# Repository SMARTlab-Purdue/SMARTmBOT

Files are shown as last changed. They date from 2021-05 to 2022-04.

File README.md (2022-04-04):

# SMART lab multi-roBOT (SMARTmBOT)
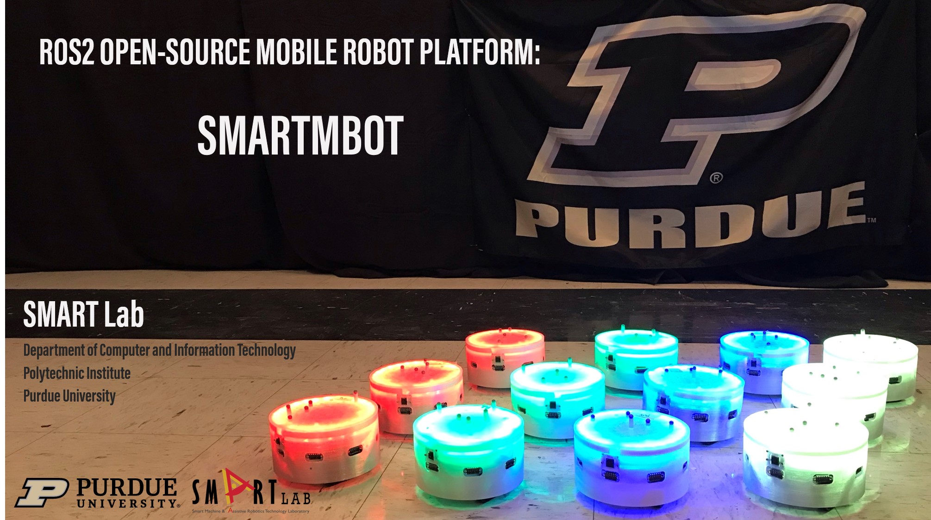
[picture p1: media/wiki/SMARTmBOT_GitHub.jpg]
GitHub markdown


## Objectives
The goal of this repository is to introduce a new, customizable, scalable, and fully opensource mobile robot platform, called SMARTmBOT (v2022). In this repository, we provide a detailed tutorial, and all design files and source codes so that you can build your own SMARTmBOT with off-the-shelf components and also customize its design and functionalities according to your needs. SMARTmBOT supports a new Robot Operating System 2 (ROS2) on Raspberry Pi 4, and we expect SMARTmBOT to be definitely useful for studying the basics of robotics, especially mobile robotics. SMARTmBOT can also be used to study advanced topics such as swarm robotics.

## Wiki, Tutorial, and Demonstrations
Please refer to our [Wiki page](https://github.com/SMARTlab-Purdue/SMARTmBOT/wiki) for a detailed tutorial on SMARTmBOT. The content of the tutorial is as follows:

1. [Basic ROS2 Example](https://github.com/SMARTlab-Purdue/SMARTmBOT/wiki/1.-Basic-ROS2-Example)

2. [Build SMARTmBOT (Hardware)](https://github.com/SMARTlab-Purdue/SMARTmBOT/wiki/2.-Build-SMARTmBOT-(Hardware))

3. [Build SMARTmBOT (Software)](https://github.com/SMARTlab-Purdue/SMARTmBOT/wiki/3.-Build-SMARTmBOT-(Software))

4. [SMARTmBOT Examples](https://github.com/SMARTlab-Purdue/SMARTmBOT/wiki/4.-SMARTmBOT-Examples)

You can also read or download a PDF version of [SMARTmBOT Guide/Manual](https://github.com/SMARTlab-Purdue/SMARTmBOT/blob/main/Documents/SMARTmBOT_Manual.pdf), and watch a full demo video of the SMARTmBOT at <https://youtu.be/uniaTWcCeDM>.

## Contact
If you have any questions or find any issues on SMARTmBOT, please feel free to contact us. We will fix and update them as soon as possible.

## Contributors
All of the contributors are with [SMART Lab](http://www.smart-laboratory.org/index.html), Department of Computer and Information Technology, Purdue University, West Lafayette, IN 47907, USA.<br />

<table>
  <tr>

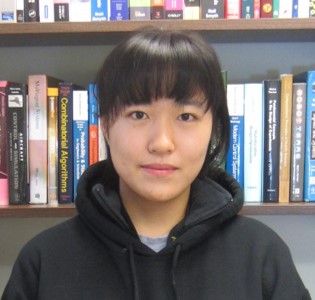
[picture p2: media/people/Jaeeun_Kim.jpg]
<td align="center"><a href="http://www.smart-laboratory.org/group/Jaeeun_Kim.html"><br />
              <sub><b><a href="http://www.smart-laboratory.org/group/Jaeeun_Kim.html" title="personal_website">🌍Jaeeun Kim</b></sub></a><br />
<sub><b>Software</b></sub></a><br />
<sub><b><a href="mailto: kim2592@purdue.edu" title="contact">kim2592@purdue.edu </a></b></sub></a><br />

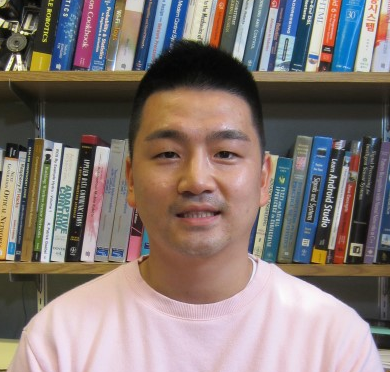
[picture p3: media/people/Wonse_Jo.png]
<td align="center"><a href="http://www.smart-laboratory.org/group/Wonse_Jo.html"><br />
          <sub><b><a href="http://www.smart-laboratory.org/group/Wonse_Jo.html" title="personal_website">🌍Wonse Jo</b></sub></a><br />
<sub><b>Hardware</b></sub></a><br />
<sub><b><a href="mailto: jow@purdue.edu" title="contact">jow@purdue.edu</a></b></sub></a><br />
</td>
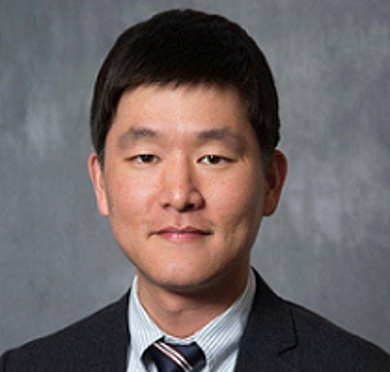
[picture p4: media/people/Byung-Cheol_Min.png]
<td align="center"><a href="http://www.smart-laboratory.org/group/bcm.html"><br />
  <sub><b><a href="http://www.smart-laboratory.org/group/bcm.html" title="personal_website">🌍Byung-Cheol Min</b></sub></a><br />
<sub><b>Director</b></sub></a><br />
<sub><b><a href="mailto: minb@purdue.edu" title="contact">minb@purdue.edu</a></b></sub></a><br />

  </tr>

</table>

## Acknowledgement

This material is based upon work supported by the National Science Foundation under [Grant No. IIS-1846221](https://www.nsf.gov/awardsearch/showAward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). Any opinions, findings, and conclusions or recommendations expressed in this material are those of the author(s) and do not necessarily reflect the views of the National Science Foundation.

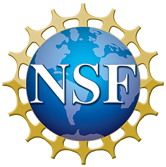
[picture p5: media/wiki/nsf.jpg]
NSF_image


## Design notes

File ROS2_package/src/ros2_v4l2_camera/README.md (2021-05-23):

# v4l2_camera

A ROS 2 camera driver using Video4Linux2 (V4L2).

## Installation
[This article](https://medium.com/swlh/raspberry-pi-ros-2-camera-eef8f8b94304) details how to build and run this package. It focuses on Raspberry Pi OS with the Raspberry Pi Camera Module V2 but should generalise for most systems.

### ROS package install
This is available from the ROS package repositories and can therefore be installed with the following command and your ROS version name:

    apt-get install ros-<ros_version>-v4l2-camera

### Building from source
If you need to modify the code or ensure you have the latest update you will need to clone this repo then build the package.

    $ git clone --branch foxy https://gitlab.com/boldhearts/ros2_v4l2_camera.git src/v4l2_camera
    $ colcon build

Most users will also want to set up compressed transport using the dependencies below.

### Usage
Publish camera images, using the default parameters:

        ros2 run v4l2_camera v4l2_camera_node

Preview the image (open another terminal):

        ros2 run rqt_image_view rqt_image_view

## Dependencies

* `image_transport` - makes it possible to set up compressed transport
  of the images, as described below.

    The ROS 2 port of `image_transport` in the `image_common`
    repository is needed inside of your workspace:

        git clone --branch ros2 https://github.com/ros-perception/image_common.git src/image_common

    Note that `image_transport` only supports raw transport by default
    and needs additional plugins to actually provide compression; see
    below how to do this.

## Nodes

### v4l2_camera_node

The `v4l2_camera_node` interfaces with standard V4L2 devices and
publishes images as `sensor_msgs/Image` messages.

#### Published Topics

* `/raw_image` - `sensor_msgs/Image`

    The image.

#### Parameters

* `video_device` - `string`, default: `"/dev/video0"`

    The device the camera is on.

* `pixel_format` - `string`, default: `"YUYV"`

    The pixel format to request from the camera. Must be a valid four
    character '[FOURCC](http://fourcc.org/)' code [supported by
    V4L2](https://linuxtv.org/downloads/v4l-dvb-apis/uapi/v4l/videodev.html)
    and by your camera. The node outputs the available formats
    supported by your camera when started.  
    Currently supported: `"YUYV"` or `"GREY"`

* `output_encoding` - `string`, default: `"rgb8"`

    The encoding to use for the output image.  
    Currently supported: `"rgb8"`, `"yuv422"` or `"mono8"`.

* `image_size` - `integer_array`, default: `[640, 480]`

    Width and height of the image.

* Camera Control Parameters

    Camera controls, such as brightness, contrast, white balance, etc,
    are automatically made available as parameters. The driver node
    enumerates all controls, and creates a parameter for each, with
    the corresponding value type. The parameter name is derived from
    the control name reported by the camera driver, made lower case,
    commas removed, and spaces replaced by underscores. So
    `Brightness` becomes `brightness`, and `White Balance, Automatic`
    becomes `white_balance_automatic`.

## Compressed Transport

By default `image_transport` only supports raw transfer, plugins are
required to enable compression. Standard ones are available in the
[`image_transport_plugins`](https://github.com/ros-perception/image_transport_plugins)
repository. These depend on the OpenCV facilities provided by the
`vision_opencv` repository. You can clone these into your workspace to
get these:

    cd path/to/workspace
    git clone https://github.com/ros-perception/vision_opencv.git --branch ros2 src/vision_opencv
    git clone https://github.com/ros-perception/image_transport_plugins.git --branch ros2 src/image_transport_plugins

### Building: Ubuntu

The following packages are required to be able to build the plugins:

    sudo apt install libtheora-dev libogg-dev libboost-python-dev

### Building: Arch

To get the plugins compiled on Arch Linux, a few special steps are
needed:

* Arch provides OpenCV 4.x, but OpenCV 3.x is required
* Arch provides VTK 8.2, but VTK 8.1 is required
* `boost-python` is used, which [needs to be linked to python libs
  explicitly](https://bugs.archlinux.org/task/55798):

        colcon build --symlink-install --packages-select cv_bridge --cmake-args "-DCMAKE_CXX_STANDARD_LIBRARIES=-lpython3.7m"

### Usage

If the compression plugins are compiled and installed in the current
workspace, they will be automatically used by the driver and an
additional `/image_raw/compressed` topic will be available.

Neither Rviz2 or `showimage` use `image_transport` (yet). Therefore, to
be able to view the compressed topic, it needs to be republished
uncompressed. `image_transport` comes with the `republish` node to do
this:

    ros2 run image_transport republish compressed in/compressed:=image_raw/compressed raw out:=image_raw/uncompressed

The parameters mean:

* `compressed` - the transport to use for input, in this case
  'compressed'. Alternative: `raw`, to republish the raw `/image_raw`
  topic
* `in/compressed:=image_raw/compressed` - by default, `republish` uses
  the topics `in` and `out`, or `in/compressed` for example if the
  input transport is 'compressed'. This parameter is a ROS remapping
  rule to map those names to the actual topic to use.
* `raw` - the transport to use for output. If omitted, all available
  transports are provided.
* `out:=image_raw/uncompressed` - remapping of the output topic.

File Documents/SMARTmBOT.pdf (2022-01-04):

## A ROS2-based Swarm Robot Platform: SMARTmBOT

Jaeeun Kim, Wonse Jo, and Byung-Cheol Min

Abstract— This paper is to introduce a new open-source swarm robot platform for a multi-robot research applications. The mobile robot is 15 cm in diameter and 10 cm in height and supports the Robot Operating System 2 (ROS2). The hardware is composed of three layers of printed circuit board (PCB). The first PCB layer has two DC motors with a motor driver chip (L293D), and two line sensors to detect cliffs or black lines. The second PCB layer is to connect with a Raspberry Pi and eight times-of-flight (ToF) sensors to detect surrounding obstacles. The third PCB layer is customizable. In our case, we mounted four RGB SMD LEDs (SMD5050), RGB LED strips (WS2913b), and a speaker on the thrid PCB layer. Therefore, the robot platform is able to change its light either individually or as a whole, play music, and measure the distance of nearby obstacles using ToF sensors. Furthermore, we provide all source codes and design files used on the mobile robot platform.

I. INTRODUCTION

Swarm robotics is a potential field that can solve complex and difficult challenges in robotics applications. Various robot platforms have been introduced by companies and research groups for swarm robotics.
To address these challenges, various research institutes, universities, and companies have been launching various STEM tools. An example of the mobile robot platforms is Donkey Car, which provides the learning tools for driving an RC car and process data collected with it [1]. Similarly, Miniskybot aims to be a learning tool that is cheap and easy to build [2]. It has 3D printed parts and its own processing board, which is controlled by a personal computer. Although there are aforementioned mobile platforms that allow the user to build from scratch and modify as they need, there is still a huge barrier for students to learn STEM educations, as well as for the researchers who are not in robotics to conduct human-robot interaction (HRI).
However, those platforms are still expensive and limited in expandability for other research to use.
Therefore, we propose a new fully open-source swarm robot platform, called SMARTmBOT that can be used for swarm research purposes. The SARTmBOT is made with a 3D printed casing and using a Raspberry Pi 4 installed Robot Operating System 2 (ROS2) [3] to control the devices and read sensors mounted on three layers of the printed circuit board (PCB). The sensors and visual output components are mounted on the PCBs, such as RGB LEDs, Time of Flight (ToF) sensors, photo reflector sensors (also known as a line sensor), and DC gear motors. The power source for

Jaeeun Kim, Wonse Jo, and Byung-Cheol Min are with SMART Lab, Department of Computer and Information Technology, Purdue University, West Lafayette, IN 47907, USA kim2592@purdue.edu, jow@purdue.edu, minb@purdue.edu

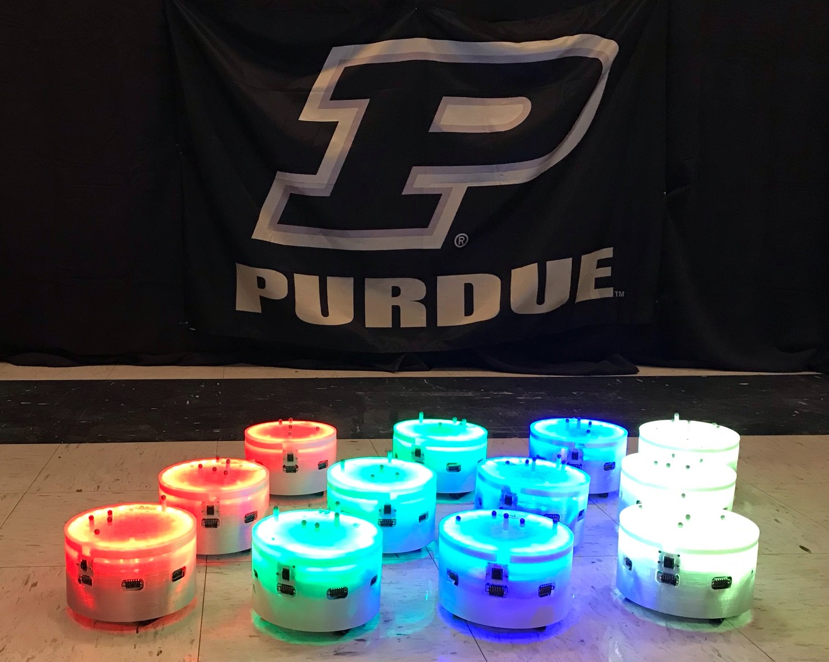
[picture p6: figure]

Fig. 1: SMARTmBOT platforms mounted a WS2813B RGB LED strip to change the overall case.

SMARTmBOT is a portable power bank, and the rest of the sensors and components are powered by the Raspberry Pi 4. As well, we elaborated specific details of software in Section III.

II. HARDWARE
The components used in the SMARTmBOT are shown in Table I, composed of off-the-shelf items. The cost for building a SMARTmBOT is about $ 250. Furthermore, in order to assist those who are building the robot, a video to introduce how to solder and assembly the platform is available. To find the video, please go to this link: https:
//youtu.be/hEa0x9cL72s
A. 3D designs
The SMARTmBOT is 15 cm in diameter and 10 cm in height, and composed of 3D printed parts as shown in Figure 3. All parts should be completely printed and soldered before assembling them. Figure 3a is a transparent case to cover the whole robot platform and illuminate color lights using RGB LEDs. Figure 3b is a power bank holder that serves as the main base of the SMRTmBOT. The part is to mount the power bank and connect other PCB layers and Raspberry Pi 4. Figure 3c is a motor mount bracket to fix two DC motors. The perforated hole is to pass and arrange a power cable and cables of the DC motors. Figure 3d is a shaft support bracket to fasten the the shaft of belt chain on the power bank holder. Figure 3e is a motor mount bracket to fix a Pi camera

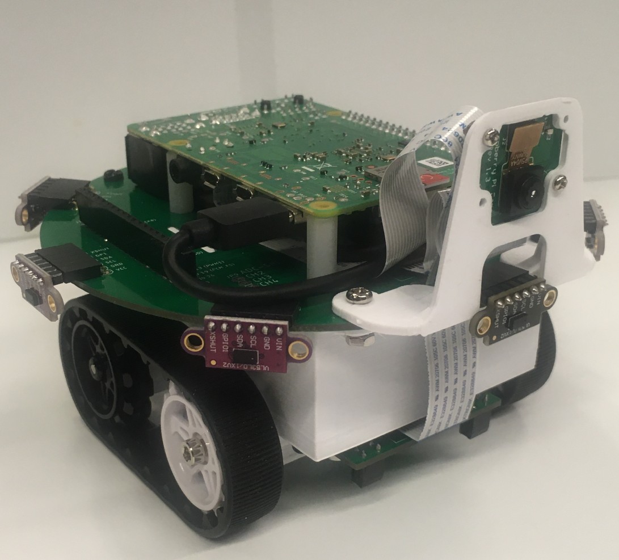
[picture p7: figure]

Fig. 2: Basic version of the SMARTmBOT platform.

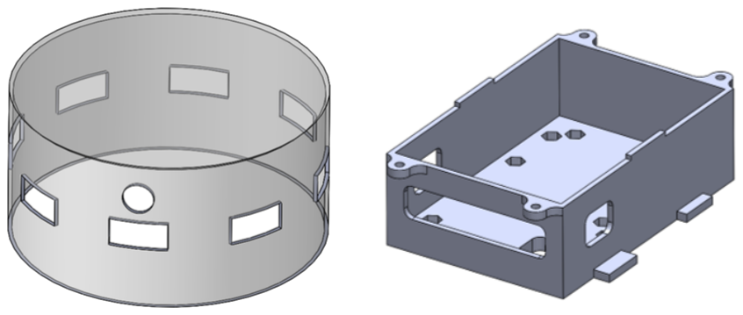
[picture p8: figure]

(a) (b)
(c) | (d) | (e)

Fig. 3: 3D printing parts for SMARTmBOT; (a) Transparent case (1EA), (b)Power bank holder, (c) Motor mount bracket,
(d) Shaft support bracket, and (e) Camera holder.

on the second PCB layer. All design and 3D printing files can be downloaded from: https://github.
com/SMARTlab-Purdue/SMARTmBOT/tree/main/ Hardware_design/3DprintingParts.
B. PCB design
1) First Layer: The first PCB layer shown in Figure 4a is located between the wheels, facing downwards. It includes a motor driver (L293D), ADC-SPI chip (MCP3008), and two photo reflector sensors (RPR220). Motor lines and external power supply from the battery is connected to this layer.
2) Second Layer: The second layer is placed on top of the battery housing, holding mounts for Raspberry Pi and ToF sensors.
3) Third Layer: The third layer is placed on top of the second layer, connected by pin headers.
4) Custom Layer: This layer provides extra pins on the third layer PCB to connect an additional layers.

TABLE I: BOM list for the SMARTmBOT

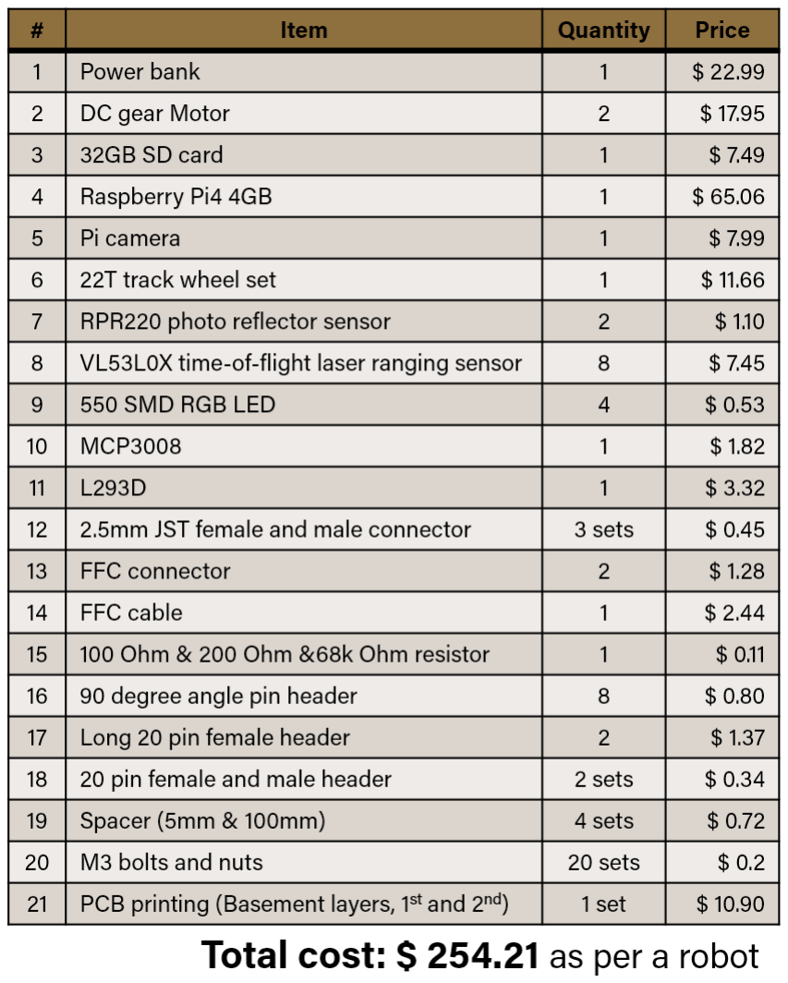
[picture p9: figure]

III. SOFTWARE

The software required to run the ROS2 packages are available for download at https://github.com/
SMARTlab-Purdue/smart_mbot_ws. (https://github.com/SMARTlab-Purdue/smart_mbot_ws) The system runs
on Ubuntu 20.04 Server and ROS2 Galactic.
A. Control the LEDs with GPIO Pins

The LEDs can emit red, green, or blue light. Each color is connected to a separate GPIO pin, so the user can turn individual or multiple colors at the same time. The pins used for the LEDs are 7, 8, and 25. Below is the part of LED code included in the package. To control the LED colors, set the output of the wanted color’s pin to HIGH by changing the GPIO.LOW to GPIO.HIGH.

Code 1: Python example

1 GPIO.output(pin, GPIO.LOW)

B. Read ADC via SPI Node

The photo reflector sensors used in this robot, RPR220, are analog sensors which signals are converted into digital signals and read on SPI bus via MCP3008 chip. The pin used for the sensor is 5.
The code in the package will convert the analog data to voltage values, stored in an array. Below is the part of the

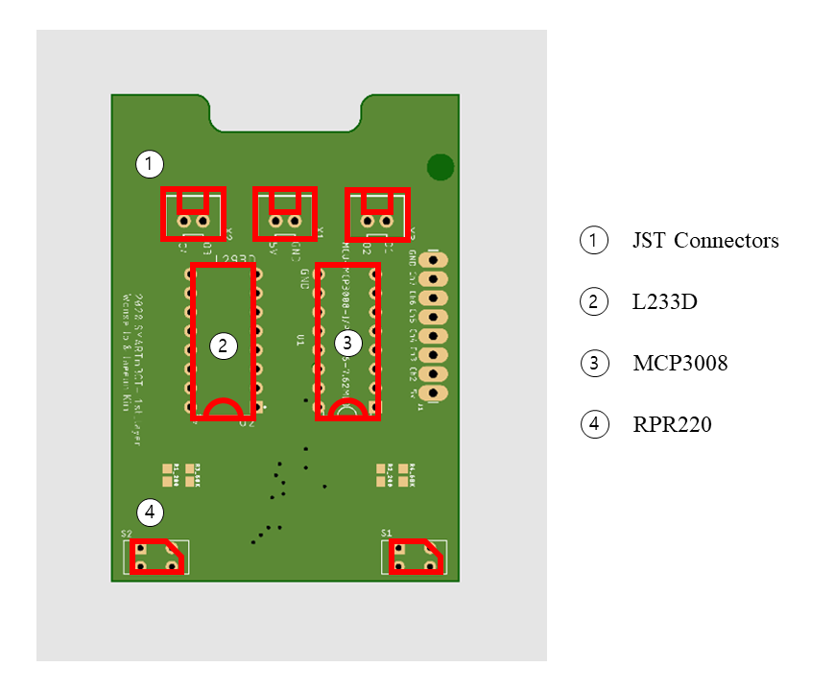
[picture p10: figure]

(a) First PCB layer

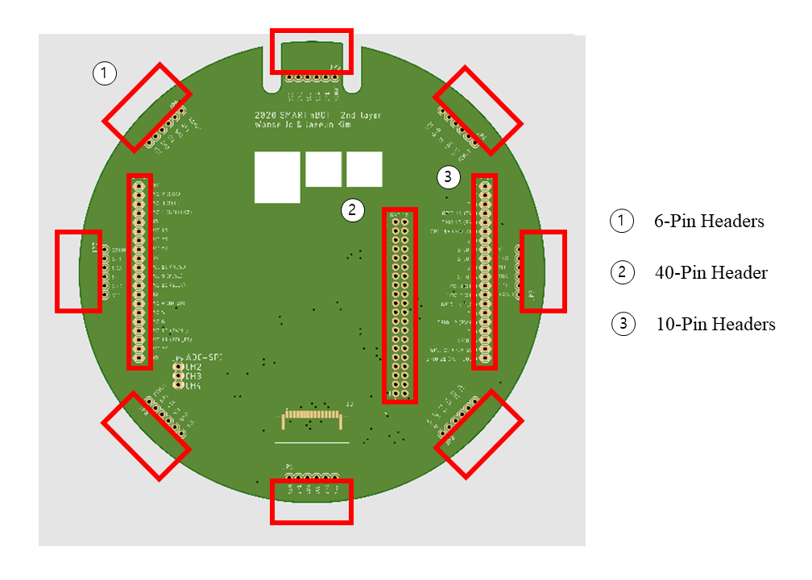
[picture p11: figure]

(b) Second PCB layer

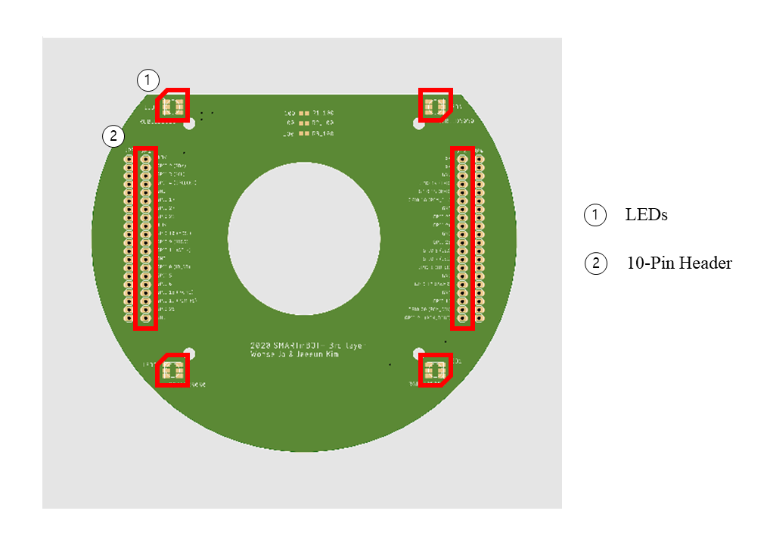
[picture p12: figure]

(c) Third PCB layer

Fig. 4: Gerber design files for the PCB layers;

code used for reading data from the sensors. The data is automatically published as ROS2 message Float32MultiArray as ’smartmobil/ADC’.

Code 2: Python example

1 | # Initialize and define Publishers
2 | self.pub_adc_spi_reader = self.create_publisher(
| Float32MultiArray, ’smartmobil/ADC’, 10)

3
4 | # Setting timer for publisher
5 | pub_adc_spi_reader_timer_period = 0.001 #sec
6 | self.pub_adc_spi_reader_timer =
7 | self.create_timer(pub_adc_spi_reader_timer_period,
| self.pub_adc_spi_reader_timer_callback)

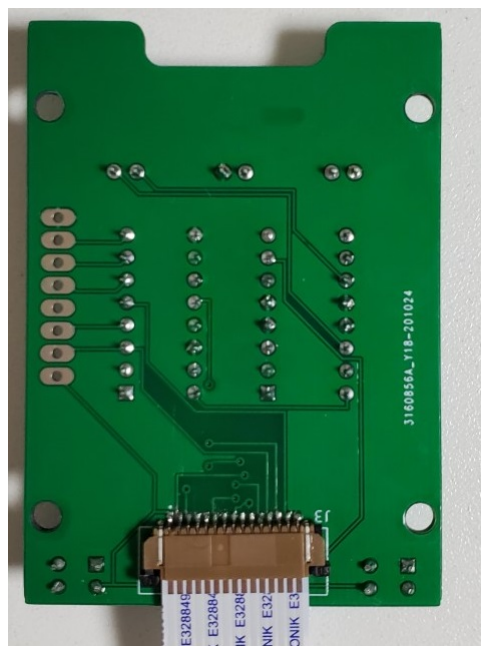
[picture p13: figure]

(a) Back of the first layer

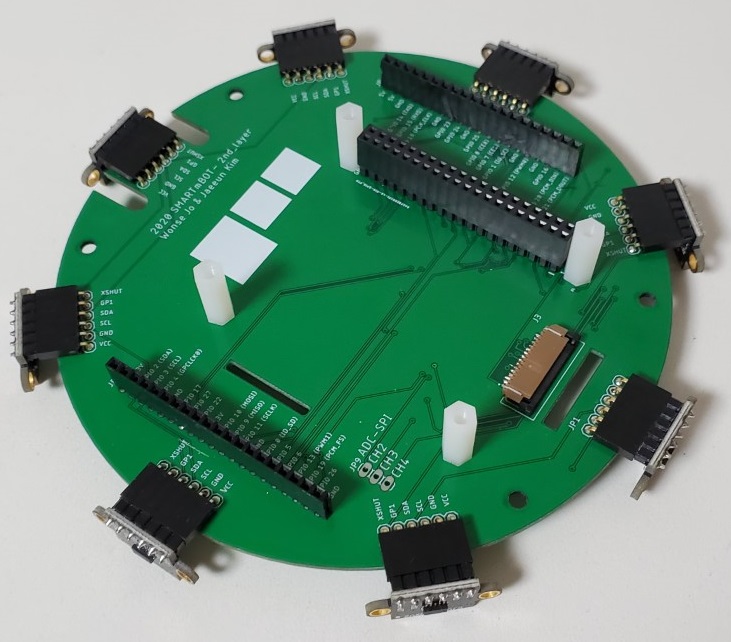
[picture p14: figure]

(b) Isometric view of the second layer

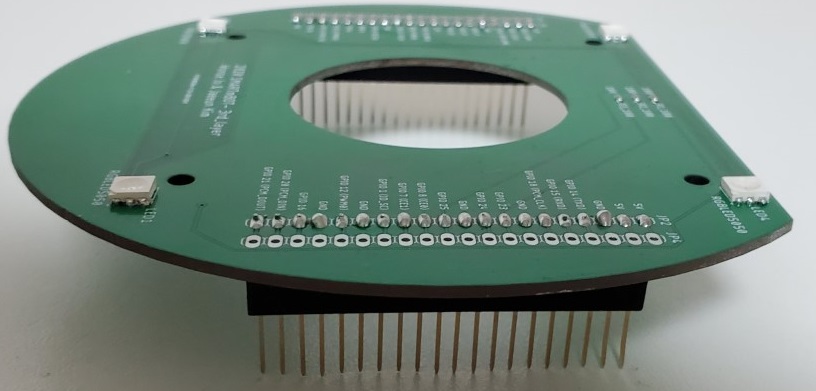
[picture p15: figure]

(c) Isometric view of the third view

Fig. 5: Three simple graphs

C. Control DC Motors
We used L293D motor driver chip to control two DC motors with pulse-width modulation (PWM). The pins used for first motor is 37, 33, 35, and second motor is 36, 38,
40. The last pins listed in each motors are used for PWM control.
The code below is displaying the equation used to calculate each wheel’s velocity with given linear and angular velocity. WHEEL BASE is the distance between the two wheels and WHEEL RADIUS is the radius of the wheel.

Code 3: Python example

1 self.right_velocity = abs((self.lin_vel - self. ang_vel * WHEEL_BASE / 2.0) / WHEEL_RADIUS)

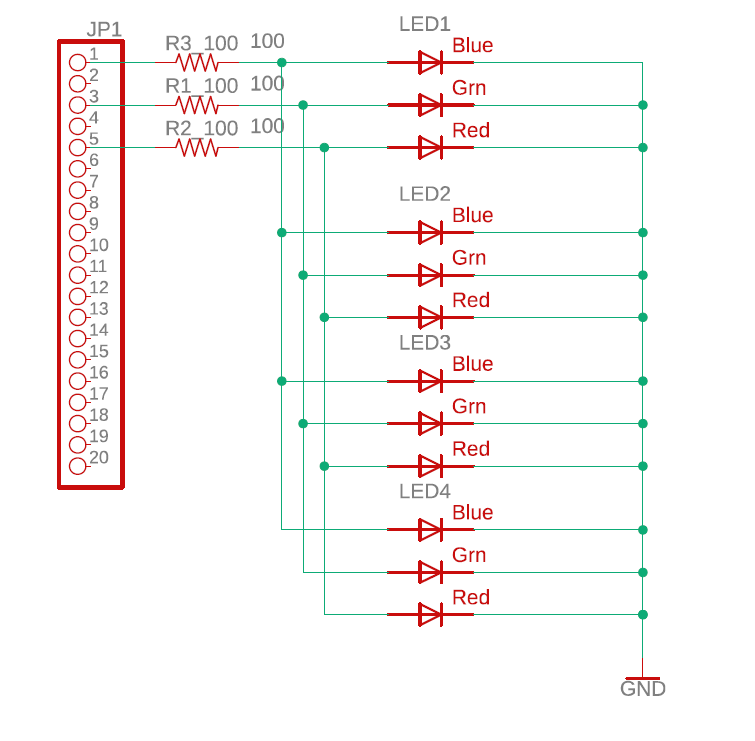
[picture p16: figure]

Fig. 6: Schematic of four LEDs (not an exhaustive diagram)

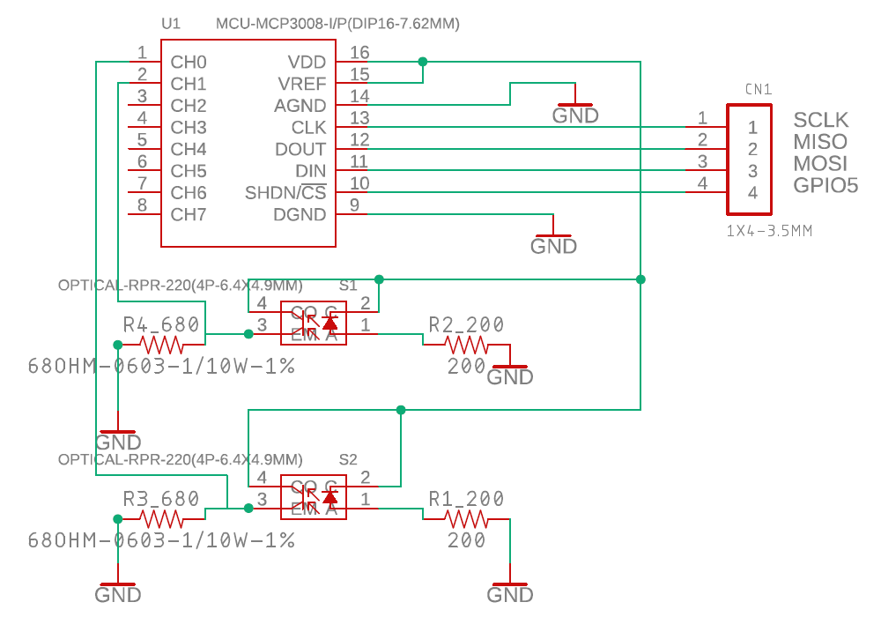
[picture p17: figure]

Fig. 7: Schematic of SPI-ADC wiring with photo reflector sensors (not an exhaustive diagram)

2 self.left_velocity = abs((self.lin_vel + self. ang_vel * WHEEL_BASE / 2.0) / WHEEL_RADIUS)

D. Read ToF Sensors
The eight ToF sensors or on a I2C bus, each with their unique I2C addresses. The pins used for the sensors are 13, 18, 16, 15, 12, 11, 8, and 10.
Below is the part of the code used for reading data from the sensors. The data is automatically published as ROS2 message Int32MultiArray as ’smartmobil/I2C’.

Code 4: Python example

1 | # Initialize the I2C module
2 | self.i2c = board.I2C()
3 | self.pub_i2c_tof_reader = self.create_publisher( Int32MultiArray, ’smartmobil/I2C’, 10)

IV. ROS 2 LAUNCH
Code 5 is a ROS2 launch file to run a group of nodes at a same time. For this application, the launch file included in the package runs motor, SPI, I²C, and LED strip nodes together.

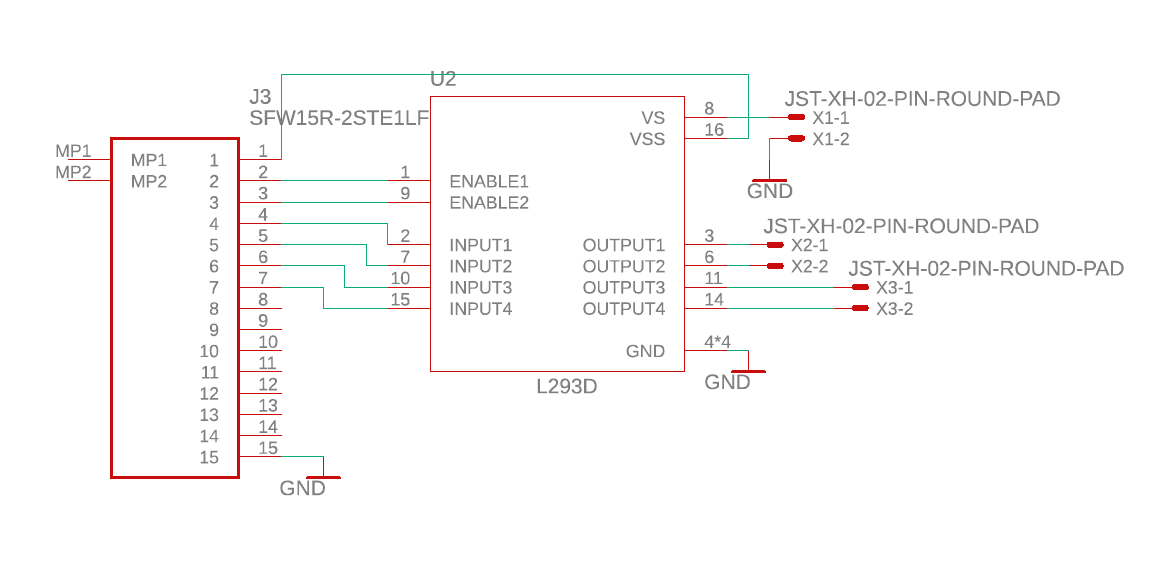
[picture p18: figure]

Fig. 8: Schematic of motor driver with two DC motors and an external power source (not an exhaustive diagram)

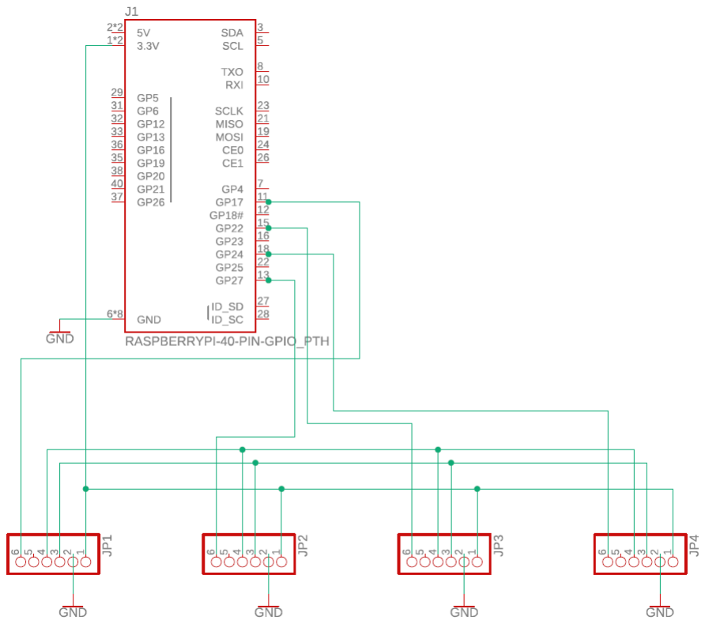
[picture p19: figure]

Fig. 9: Schematic of I2C wiring with four ToF sensors (not an exhaustive diagram)

Code 5: Launch file to control SMARTmBOT

1 import numpy as np

To launch the package, type the following commands to the terminal:

1 | $cd ˜/smart_mbot_ws
2 | $colcon build
3 | $source install/setup.bash
4 | $ros2 launch smart_mbot_pkg $smart_mbot_pkg.launch.
| py

There are two subscribers and two publishers in the package. Since they are in ROS2 message formats, the user can write to the publisher and read the publishers by accessing the topics with appropriate messages. The topics are listed and explained further in Table II and Table III.
As an example, it is possible to directly publish a message

TABLE II: ROS2 Topic Subscriber List

Name | Type | Description
/writing dc motor vel | Float32MultiArray | Linear and Angular Velocity for the Motors
/writing ws2813 rgb strip | Float32MultiArray | LED Strip Parameters

TABLE III: ROS2 Topic Publisher List

Name | Type | Description
VL53L0X tof /reading i2c | Int32MultiArray | Array of ToF Sensor Values
/reading spi adc | Float32MultiArray | Array of Photo Reflector Sensor Values

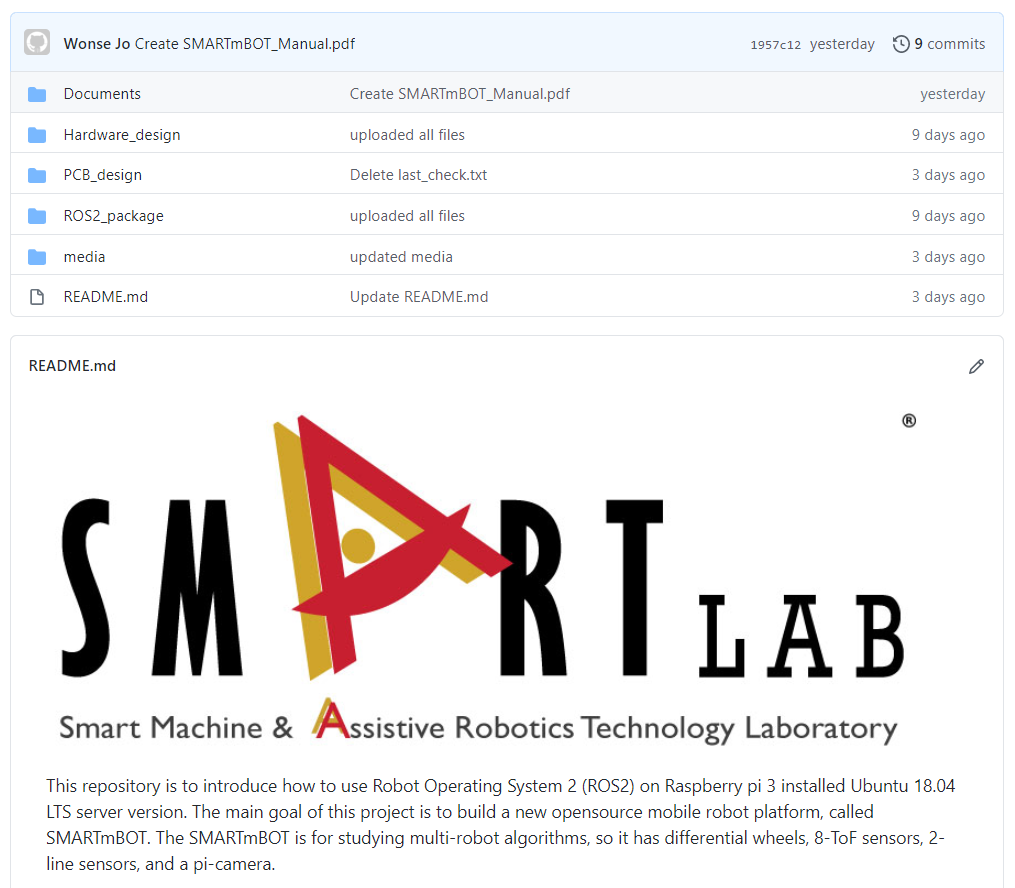
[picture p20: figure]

Fig. 10: SMARTmBOT GitHub page

to /writing dc motor vel to control the motors. The message type Float32MultiArray accepts right and left motor velocities as a form of ”data: [right motor pwm(-255 255), left motor pwm(-255 255)]”. When running in the terminal, the command should look like Code 6.

Code 6: Controlling motors of SMARTmBOT

1 | ros2 topic pub /<robot_name>/writing_dc_motor_vel std_msgs/msg/Float32MultiArray "data: [100,100]
| "
V. ONLINE REPOSITORIES
The GitHub repository can be found in the following
link: https://github.com/SMARTlab-Purdue/
SMARTmBOT. (https://github.com/SMARTlab-Purdue/SMARTmBOT) In the repository, there are 3D design CAD files, PCB design files, and ROS2 package utilized on the SMARTmBOT. The 3D design files are created by SolidWorks 2020, the PCB designs are created by AutoDesk Eagle CAD, and ROS2 nodes are written using Python 3.8.
| VI. CONCLUSION AND FUTURE WORKS
In this paper, we presented an open-source mobile robot platform to serve as a learning tool for K-12 student. The components are relatively cheap and mainstream so that they are easy to obtain, and this manual will help the students to assemble and modify the codes.
In the future, we will conduct a new user study to investigate the effect of the multi-robot system on human perception and cognition. And also, we will share the mobile platform with K-12 students to give opportunities to learn human-robot interaction via virtual meeting and/or in-person meeting.

ACKNOWLEDGMENT
This material is based upon work supported by the National Science Foundation under Grant No. IIS-1846221. Any opinions, findings, and conclusions or recommendations expressed in this material are those of the author(s) and do not necessarily reflect the views of the National Science Foundation.

REFERENCES

[1] Autorope, “donkeycar,” https://github.com/autorope/donkeycar, 2020.
[2] J. Gonzalez-Gomez, A. Valero-Gomez, A. Prieto-Moreno, and M. Abderrahim, “A new open source 3d-printable mobile robotic platform for education,” in Advances in autonomous mini robots. Springer, 2012, pp. 49–62.
[3] “Ros 2 documentation¶.” [Online]. Available: https://index.ros.org/doc/ros2/ (https://index.ros.org/doc/ros2/)

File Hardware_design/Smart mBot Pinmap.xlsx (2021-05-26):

1 | 3.3V | 5V | 2 | MOTOR
3 | SDA | 5V | 4 | SPI
5 | SCL | GND | 6 | LED
7 | 4 | 14 | 8 | I2C
9 | GND | 15 | 10 | RGB Strip
11 | 17 | 18 | 12
13 | 27 | GND | 14
15 | 22 | 23 | 16
17 | 3.3V | 24 | 18
19 | 10 | GND | 20
21 | 9 | 25 | 22
23 | 11 | 8 | 24
25 | GND | 7 | 26
27 | 0 | 1 | 28
29 | 5 | GND | 30
31 | 6 | 12 | 32
33 | 13 | GND | 34
35 | 19 | 16 | 36
37 | 26 | 20 | 38
39 | GND | 21 | 40

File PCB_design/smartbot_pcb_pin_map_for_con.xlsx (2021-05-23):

 | 1st layer to 2nd layer X1@2nd layer |  | 2nd layer to 3rd layer X2@2nd layer
P-1 | 5V | P-1 | 5V
P-2 | M1-enable | P-2 | 3.3V
P-3 | M1-input1 | P-3 | SDA
P-4 | M1-input2 | P-4 | SCL
P-5 | M2-enable | P-5 | SCLK(CLK)
P-6 | M2-input3 | P-6 | MISO(DOUT)
P-7 | M2-input4 | P-7 | MOSI(DIN)
P-8 | CLK(SCLK) | P-8 | GP4
P-9 | DOUT(MISO() | P-9 | GP6
P-10 | DIN(MOSI) | P-10 | GP12
P-11 | SHDN | P-11 | GP25
P-12 | GND | P-12 | GND

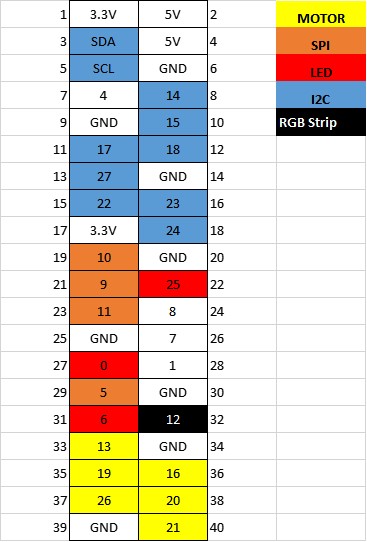
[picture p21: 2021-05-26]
media/wiki/SMARTmBOT_pinout.jpg

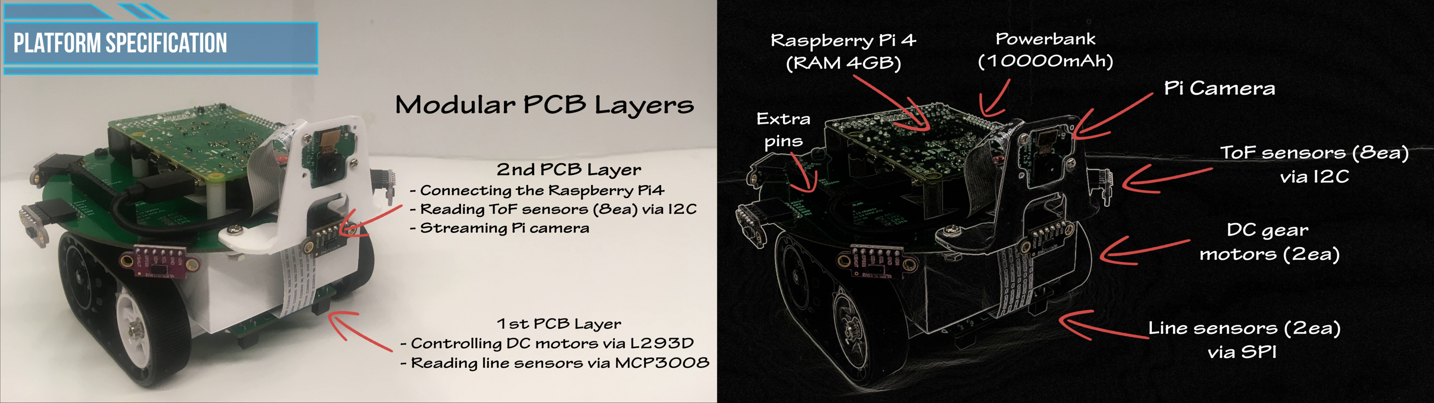
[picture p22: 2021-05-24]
media/wiki/SMARTmBOT_HARDWARE.png

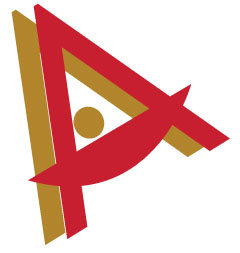
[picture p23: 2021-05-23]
PCB_design/reference/SMART-LAB_Emblem.bmp

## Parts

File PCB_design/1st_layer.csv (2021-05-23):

Part | Value | Device | Package | Description | AVAILABILITY | DESCRIPTION | DIGI-KEY_PART_NUMBER | DIGI-KEY_PURCHASE_URL | MF | MP | MPN | OC_FARNELL | OC_NEWARK | PACKAGE | PRICE | PROD_ID | VALUE
J1 |  | CONN_08LONGPADS | 1X08_LONGPADS | Multi connection point. Often used as Generic Header-pin footprint for 0.1 inch spaced/style header connections
J2 | XF2E-1215-1 | XF2E-1215-1 | XF2E-1215-1 | OMRON FPC Connector |  |  |  |  |  |  |  | unknown | unknown
R1_200 | 200 | 200OHM-0603-1/10W-1% | 0603 | 200Ω resistor |  |  |  |  |  |  |  |  |  |  |  | RES-08220 | 200
R2_200 | 200 | 200OHM-0603-1/10W-1% | 0603 | 200Ω resistor |  |  |  |  |  |  |  |  |  |  |  | RES-08220 | 200
R3_68K | 68OHM-0603-1/10W-1% | 68OHM-0603-1/10W-1% | 0603 | 68Ω resistor
R4_68K | 68OHM-0603-1/10W-1% | 68OHM-0603-1/10W-1% | 0603 | 68Ω resistor
S1 | OPTICAL-RPR-220(4P-6.4X4.9MM) | OPTICAL-RPR-220(4P-6.4X4.9MM) | SNR4-8.7X4.5X5.8MM | 314020002 |  | Reflective Optical Sensor 0.236 _6mm_ Radial - 4 Leads | 511-1366-ND | https://www.digikey.com/product-detail/en/rohm-semiconductor/RPR-220/511-1366-ND/638554 | Rohm | RPR-220 |  |  |  | Radial-4 Rohm
S2 | OPTICAL-RPR-220(4P-6.4X4.9MM) | OPTICAL-RPR-220(4P-6.4X4.9MM) | SNR4-8.7X4.5X5.8MM | 314020002 |  | Reflective Optical Sensor 0.236 _6mm_ Radial - 4 Leads | 511-1366-ND | https://www.digikey.com/product-detail/en/rohm-semiconductor/RPR-220/511-1366-ND/638554 | Rohm | RPR-220 |  |  |  | Radial-4 Rohm
U1 | MCU-MCP3008-I/P(DIP16-7.62MM) | MCU-MCP3008-I/P(DIP16-7.62MM) | DIP16-2.54-19.2X7.62MM | 310990040 | Unavailable | 10 Bit Analog to Digital Converter 4, 8 Input 1 SAR 16-PDIP |  |  | Microchip | MCP3008-I/P |  |  |  | DIP-16 Microchip | None
U2 | L293D | L293D | DIP880W50P254L2000H510Q16 | 4-Channel Motor Driver 24V 16-Pin Power PDIP Tube | Unavailable | Bipolar Motor Driver Parallel 16-PowerDIP |  |  | STMicroelectronics | L293D |  |  |  | DIP-16 STMicroelectronics | None
X1 | JST-XH-02-PIN-ROUND-PAD | JST-XH-02-PIN-ROUND-PAD | JST-XH-02-PACKAGE-ROUND-PAD | JST XH Connector 2 Pin
X2 | JST-XH-02-PIN-ROUND-PAD | JST-XH-02-PIN-ROUND-PAD | JST-XH-02-PACKAGE-ROUND-PAD | JST XH Connector 2 Pin
X3 | JST-XH-02-PIN-ROUND-PAD | JST-XH-02-PIN-ROUND-PAD | JST-XH-02-PACKAGE-ROUND-PAD | JST XH Connector 2 Pin

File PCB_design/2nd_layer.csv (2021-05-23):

Part | Value | Device | Package | Description | MF | MPN | OC_FARNELL | OC_NEWARK | POPULARITY | PROD_ID | SF_ID
J1 | RASPBERRYPI-40-PIN-GPIO_PTH | RASPBERRYPI-40-PIN-GPIO_PTH | 2X20_SHROUDED | Raspberry Pi GPIO Header |  |  |  |  |  | CONN-12263 | PRT-13054
J2 | XF2E-1215-1 | XF2E-1215-1 | XF2E-1215-1 | OMRON FPC Connector |  |  | unknown | unknown
JP1 |  | PINHD-1X6 | 1X06 | PIN HEADER
JP2 |  | PINHD-1X6 | 1X06 | PIN HEADER
JP3 |  | PINHD-1X6 | 1X06 | PIN HEADER
JP4 |  | PINHD-1X6 | 1X06 | PIN HEADER
JP5 |  | PINHD-1X6 | 1X06 | PIN HEADER
JP6 |  | PINHD-1X6 | 1X06 | PIN HEADER
JP7 |  | PINHD-1X6 | 1X06 | PIN HEADER
JP8 |  | PINHD-1X6 | 1X06 | PIN HEADER
JP_1 |  | PINHD-1X20 | 1X20 | PIN HEADER |  |  |  |  | 6
JP_2 |  | PINHD-1X20 | 1X20 | PIN HEADER |  |  |  |  | 6

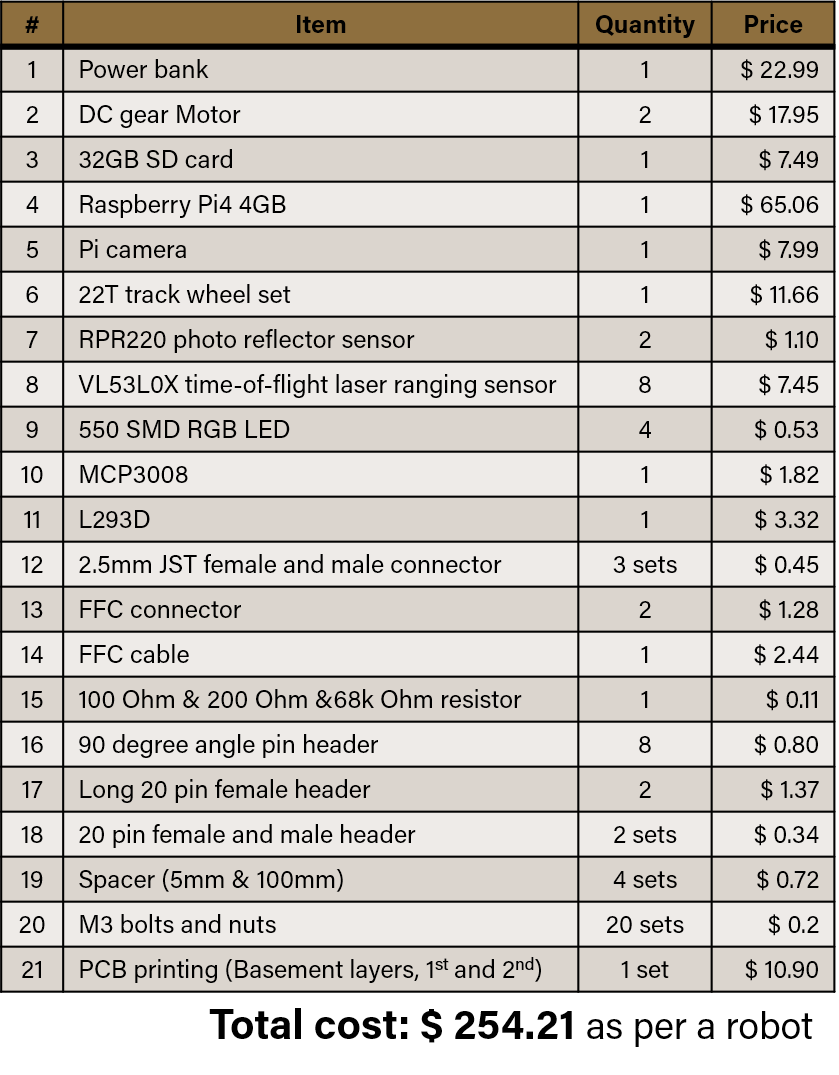
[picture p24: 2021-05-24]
media/wiki/SMARTmBOT_BOM.png

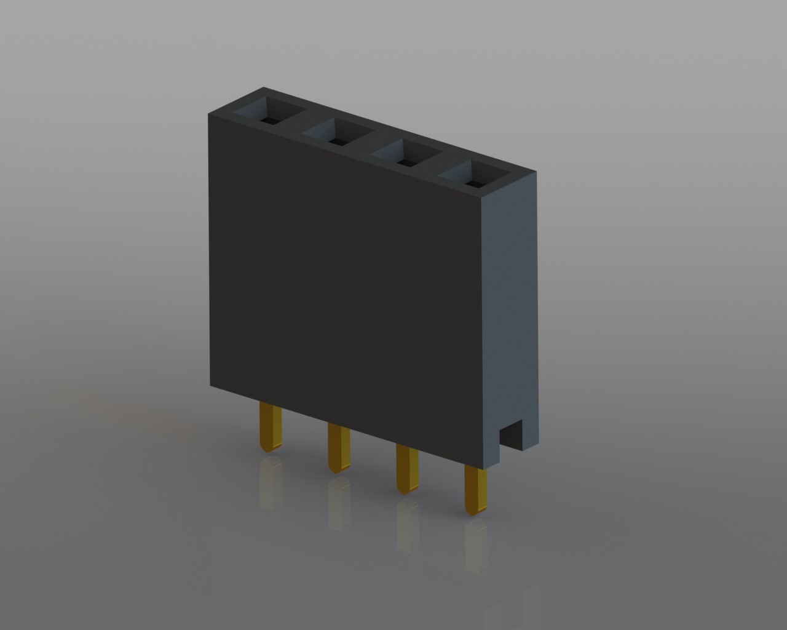
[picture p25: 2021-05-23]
Hardware_design/Components/Header Pins/Renders/header.JPG

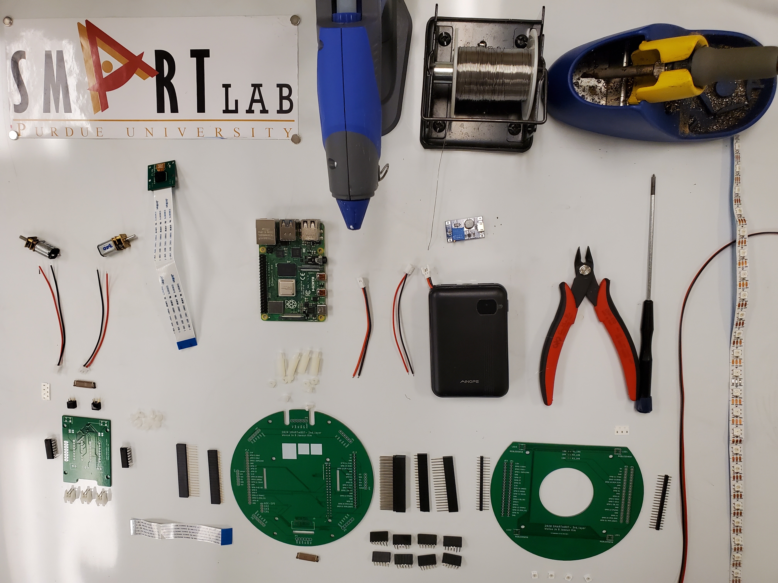
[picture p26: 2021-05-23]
media/wiki/all_parts.jpg

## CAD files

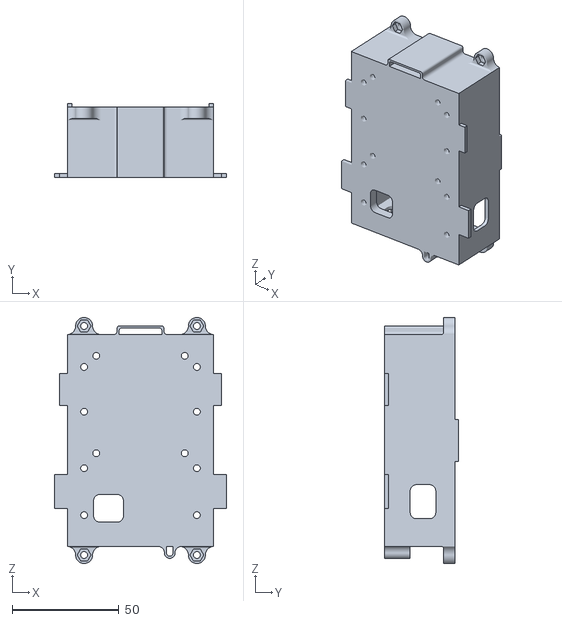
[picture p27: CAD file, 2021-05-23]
Hardware_design/3D printing Parts/main_case.STL
80.9 x 34.8 x 115.4

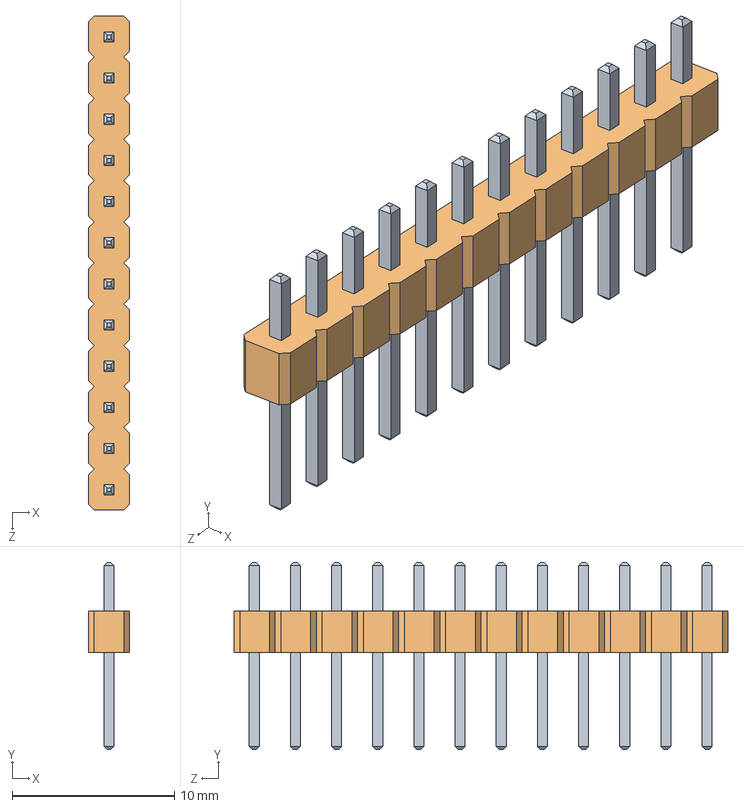
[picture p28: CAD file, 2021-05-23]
Hardware_design/Components/12x1-2-54mm-male-header-1.snapshot.12/12x1_2,54mm_male_header/12x1_male_header_pin.SLDASM
2.53 x 11.5 x 30.5 mm
pin x 12
pin_body

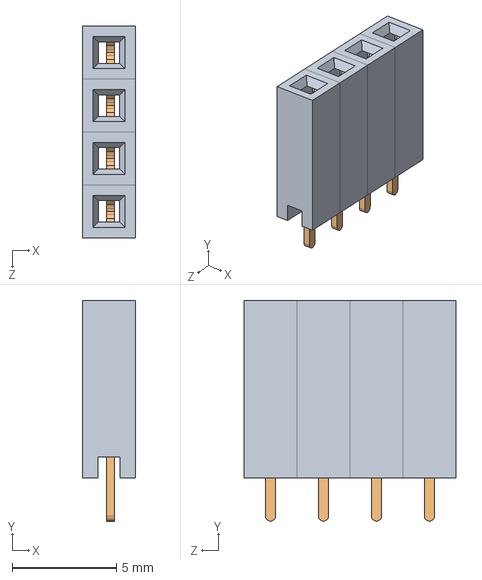
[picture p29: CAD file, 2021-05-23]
Hardware_design/Components/Header Pins/Header_4.SLDASM
2.54 x 10.6 x 10.2 mm
header x 4
pin x 4

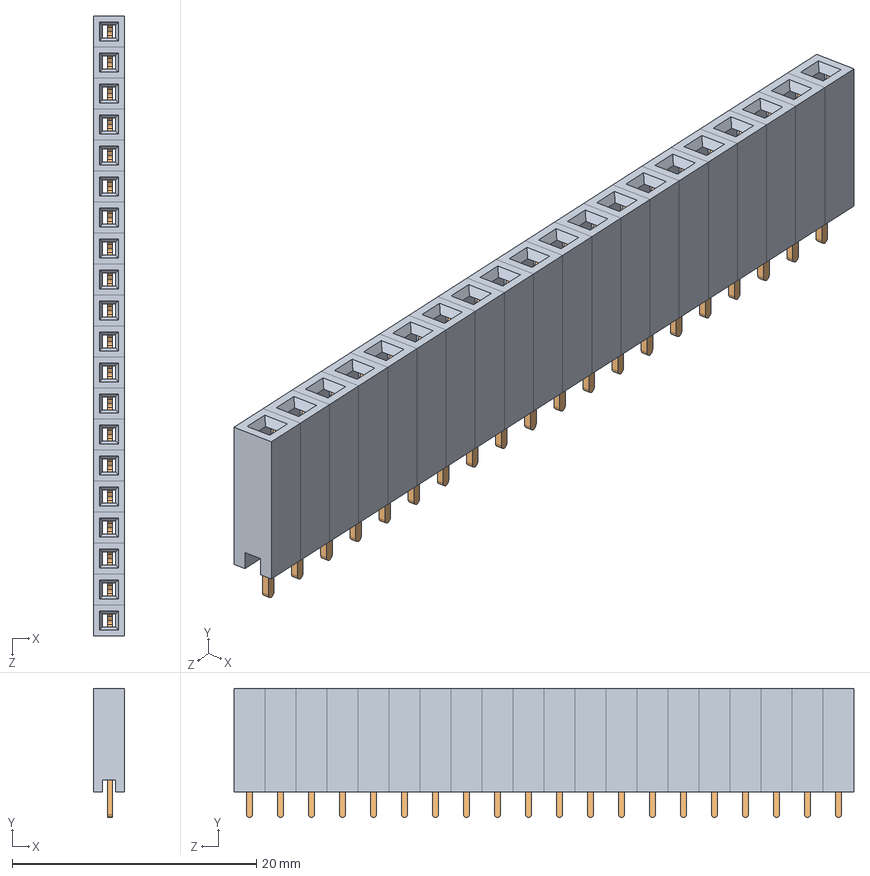
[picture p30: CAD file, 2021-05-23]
Hardware_design/Components/Header Pins/Header_1x20pin.SLDASM
2.54 x 10.6 x 50.8 mm
header x 20
pin x 20

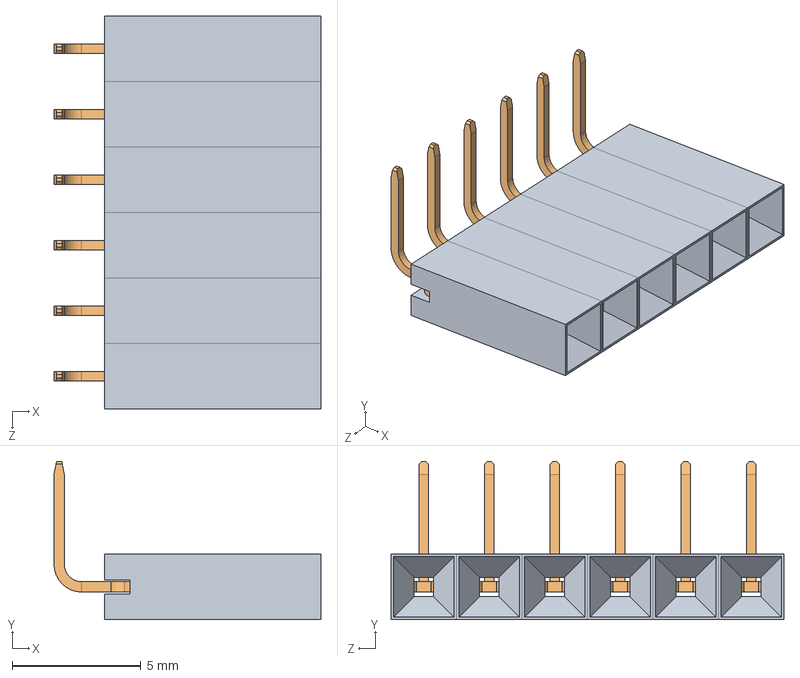
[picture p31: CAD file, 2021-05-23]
Hardware_design/Components/H254_90deg_6pin.SLDASM
10.4 x 6.14 x 15.2 mm
frame_H254 x 6
pin-90deg x 6

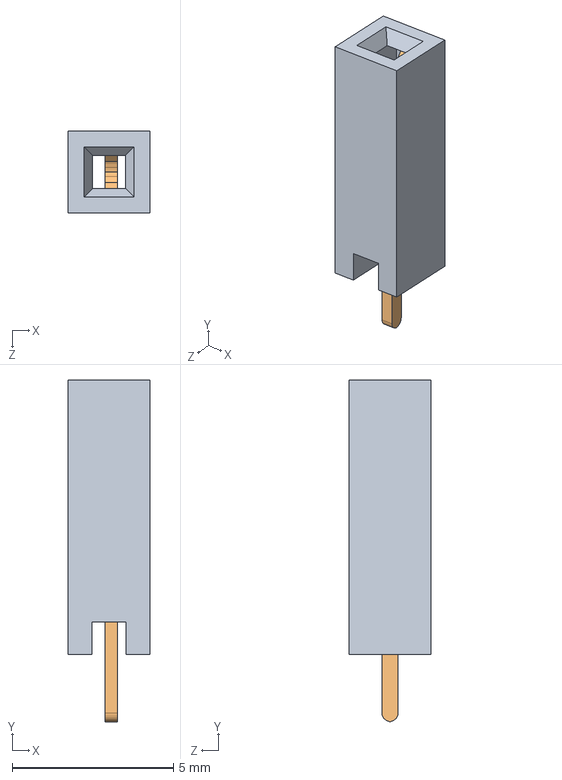
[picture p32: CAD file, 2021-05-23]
Hardware_design/Components/Header Pins/header.SLDASM
2.54 x 10.6 x 2.54 mm
header
pin

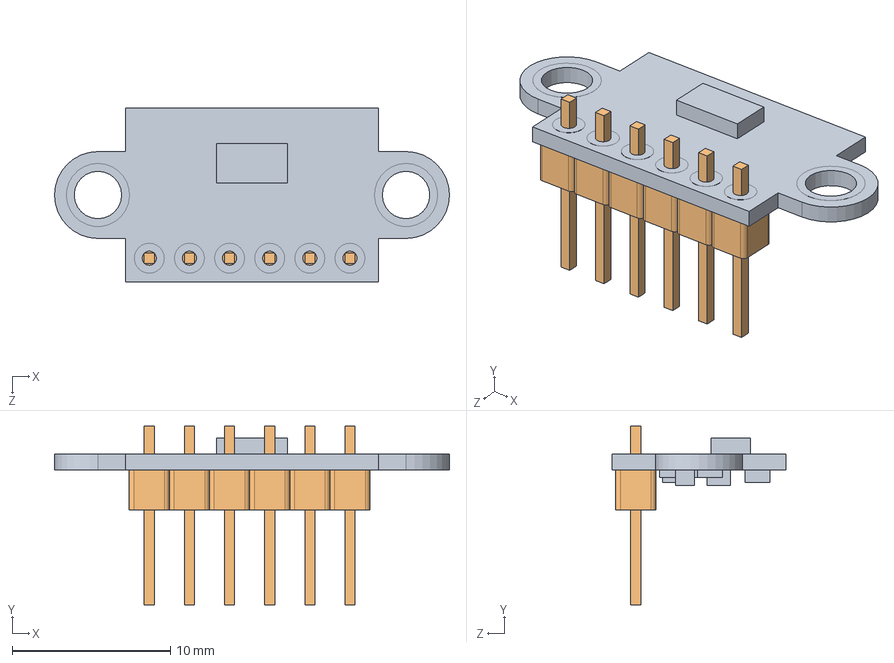
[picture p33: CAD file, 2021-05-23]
Hardware_design/Components/vl53l0x/vl53l0x.SLDASM
25.0 x 11.3 x 11.0 mm
vl53l0x_PCB
pin_header x 6

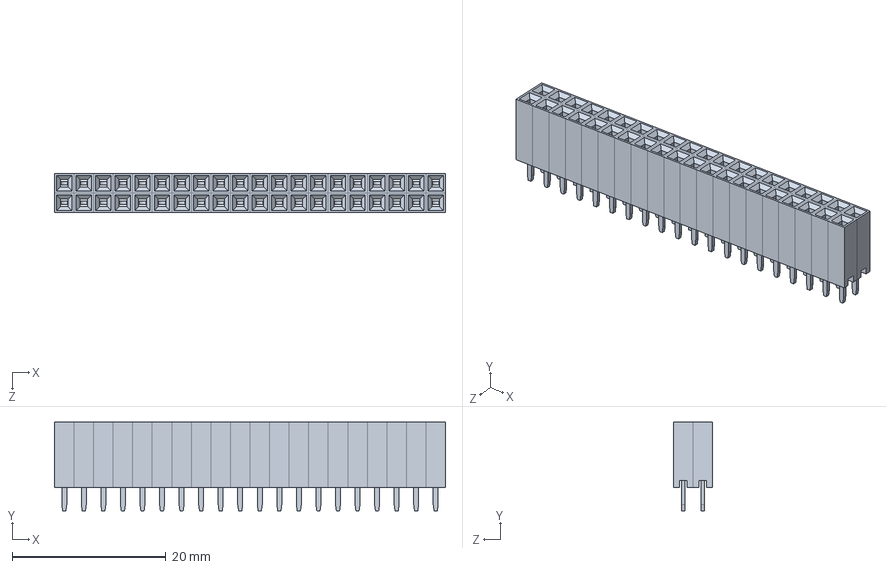
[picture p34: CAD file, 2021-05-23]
Hardware_design/Components/Buchsenleiste 2X15.SLDASM
50.8 x 11.5 x 5.08 mm
Buchsenleiste x 40

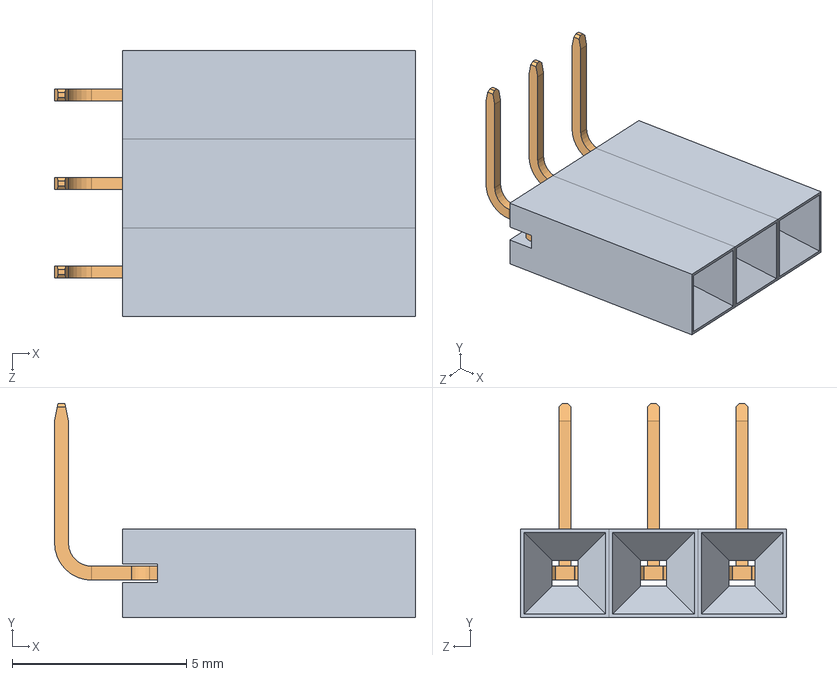
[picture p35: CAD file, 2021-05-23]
Hardware_design/Components/H254_90deg_3pin.SLDASM
10.4 x 6.14 x 7.62 mm
frame_H254 x 3
pin-90deg x 3

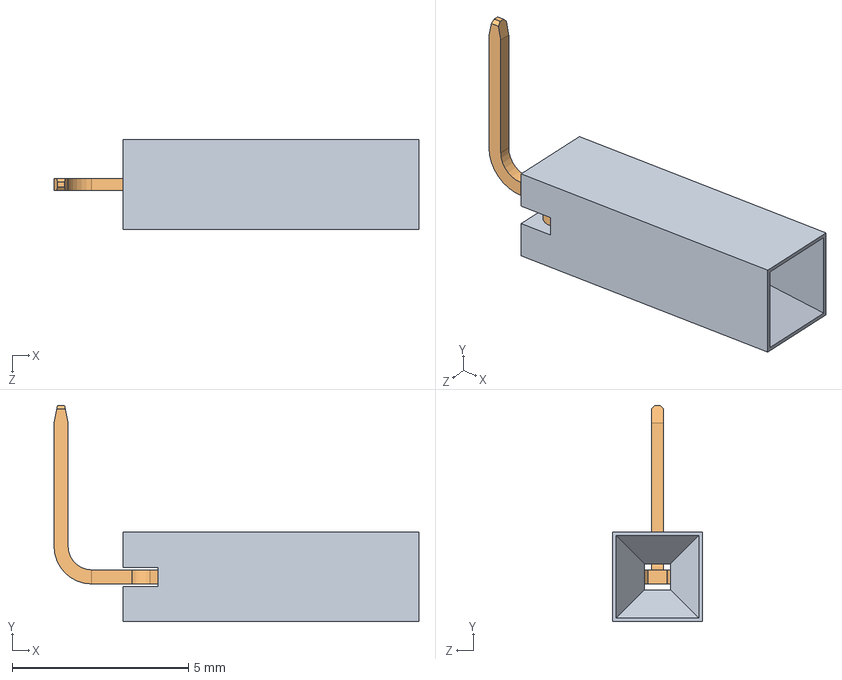
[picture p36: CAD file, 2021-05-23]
Hardware_design/Components/FrameAndPin_H254_90deg.sldasm
10.4 x 6.14 x 2.54 mm
frame_H254
pin-90deg

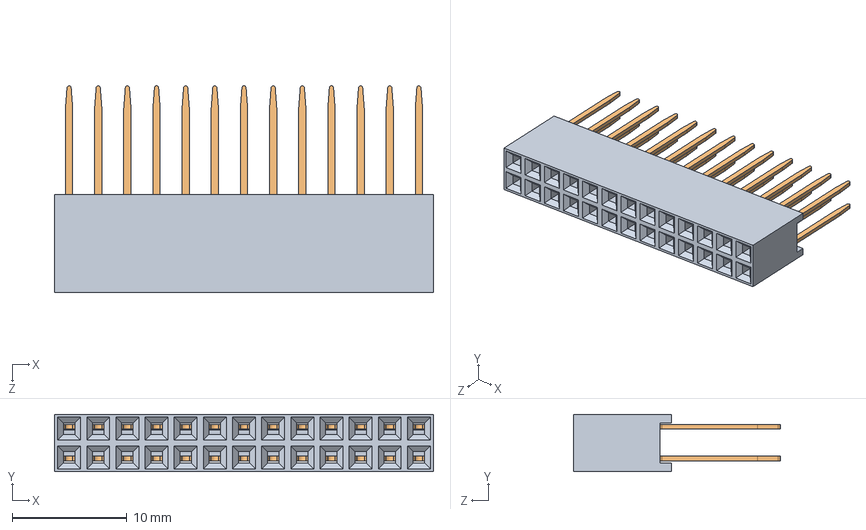
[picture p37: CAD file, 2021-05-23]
Hardware_design/Components/13x2 2,54mm Female Header/13x2_female_header.STEP
33.0 x 5.00 x 18.0 mm
Body_Varsay考an
pin_Varsay考an x 26

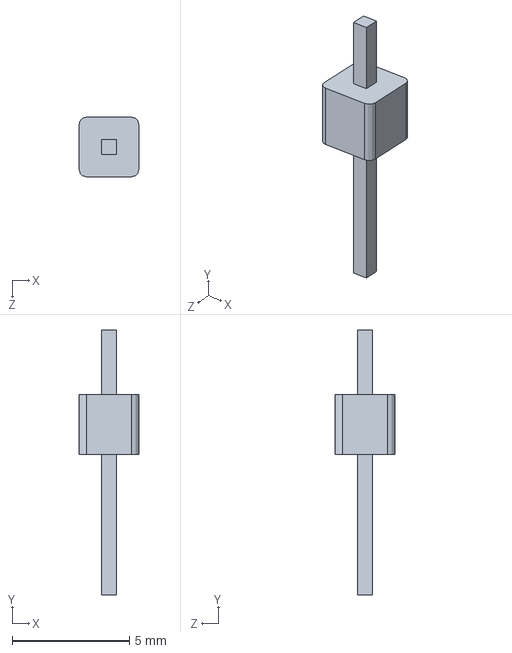
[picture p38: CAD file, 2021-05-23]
Hardware_design/Components/vl53l0x/pin_header.SLDPRT
2.54 x 11.3 x 2.54 mm

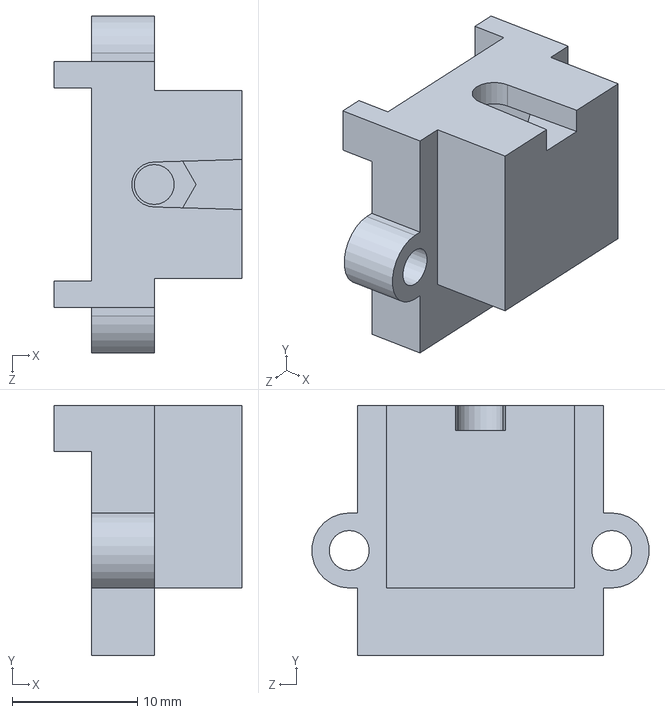
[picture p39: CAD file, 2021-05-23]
Hardware_design/Components/wheel_holder.SLDPRT
15.0 x 20.0 x 27.0 mm

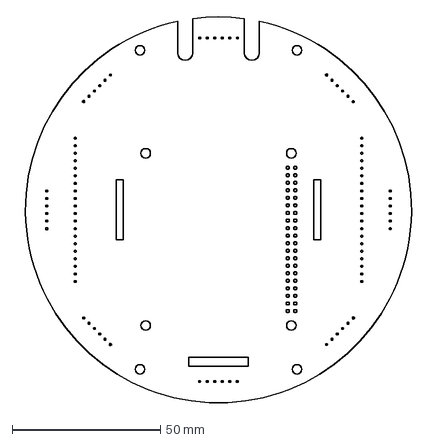
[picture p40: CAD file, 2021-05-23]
PCB_design/reference/2nd_layer.dxf
136.3 x 130.2 mm

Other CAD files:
Hardware_design/Components/main_case.SLDPRT
Hardware_design/Components/12x1-2-54mm-male-header-1.snapshot.12/12x1_male_header_pin_AP203.STEP
Hardware_design/3D printing Parts/wheel_holder_x2.STL
Hardware_design/Components/12x1-2-54mm-male-header-1.snapshot.12/12x1_2,54mm_male_header/pin_body.SLDPRT
Hardware_design/3D printing Parts/motor_holder.STL
Hardware_design/3D printing Parts/pi_cam_holder.STL
Hardware_design/Components/12x1-2-54mm-male-header-1.snapshot.12/12x1_2,54mm_male_header/pin_pin.SLDPRT
Hardware_design/Components/12x1-2-54mm-male-header-1.snapshot.12/12x1_male_header_pin_AP203.SLDASM
Hardware_design/Components/12x1-2-54mm-male-header-1.snapshot.12/12x1_male_header_pin_AP214.STEP
Hardware_design/Components/13x2 2,54mm Female Header/13x2_female_header.SLDASM
Hardware_design/Components/13x2 2,54mm Female Header/Body.SLDPRT
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

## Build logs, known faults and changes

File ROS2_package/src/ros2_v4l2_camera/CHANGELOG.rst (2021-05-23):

^^^^^^^^^^^^^^^^^^^^^^^^^^^^^^^^^
Changelog for package v4l2_camera
^^^^^^^^^^^^^^^^^^^^^^^^^^^^^^^^^

0.4.0 (2021-01-29)
------------------
* Read-only parameters as now properly marked as such
* Use C-style strings for logging macros to adapt to new formatting constraints
  See: https://index.ros.org/doc/ros2/Releases/Release-Galactic-Geochelone/#change-in-rclcpp-s-logging-macros
* Add support monochrome cameras
* Contributors: Chris Lalancette, Sander G. van Dijk, nfry321

0.3.1 (2020-11-07)
------------------
* Handle non discrete frame sizes; fixes support for Raspberry Pi + Camera Module
* Contributors: Sander G. van Dijk

0.3.0 (2020-09-26)
------------------
* Publishing is done on private topics to enable remapping of the namespace
* CameraInfo is published in intra-process communication mode
* Added parameter descriptions
* Contributors: Christian Rauch, Marcus M. Scheunemann, Sander G. van Dijk

0.2.1 (2020-08-06)
------------------
* Hold reference to parameters callback handle
* Contributors: Jacob Perron

0.2.0 (2020-06-13)
------------------
* Set frame_id on published images, default to "camera"
* Output FOURCC code of available formats
* Add parameter for setting the pixel format
  Default to using YUYV
* Contributors: Sander G. van Dijk

0.1.1 (2019-08-12)
------------------
* Add missing rclcpp_components build dependency
* Contributors: Sander G. van Dijk

0.1.0 (2019-08-11)
------------------

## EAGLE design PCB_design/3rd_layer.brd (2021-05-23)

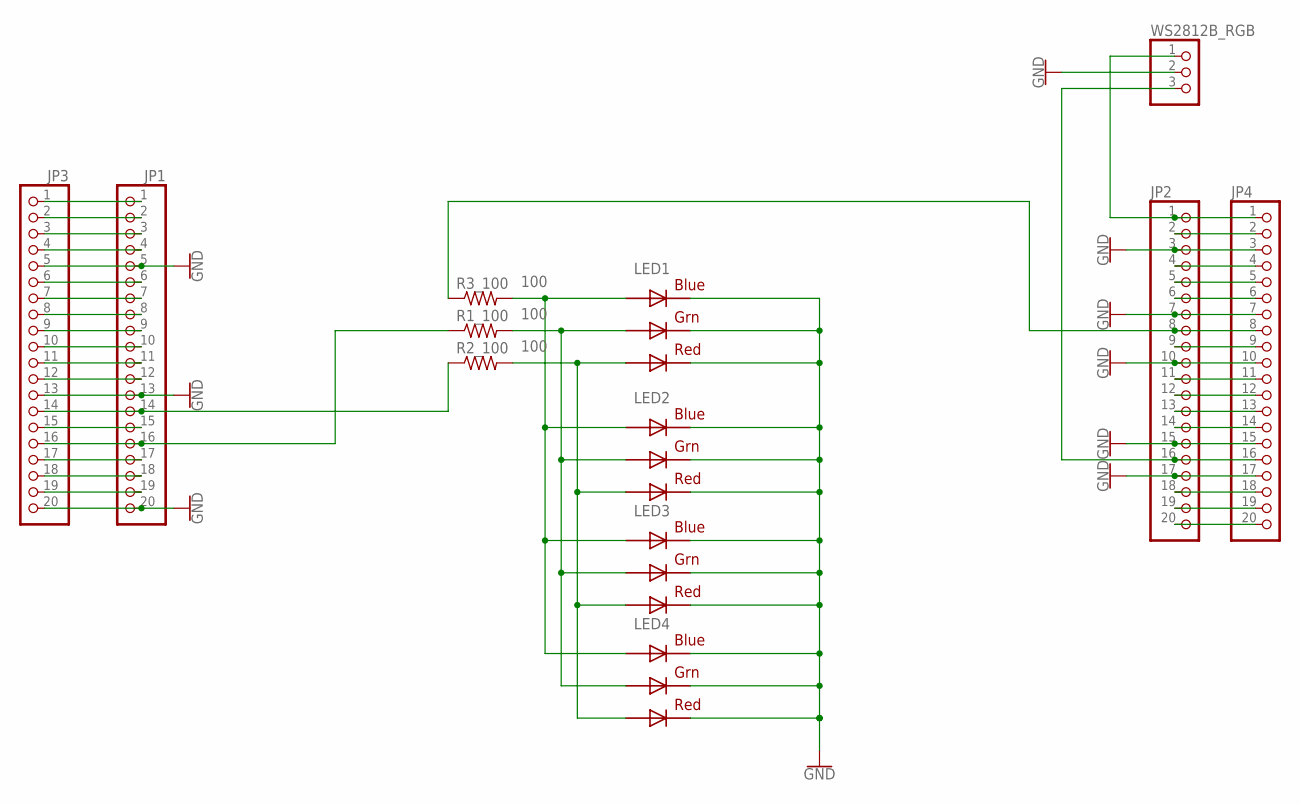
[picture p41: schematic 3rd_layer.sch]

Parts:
JP1, JP2, JP3, JP4: PINHD-1X20; 1X20
LED1, LED2, LED3, LED4: RGBLED5050
R1_100, R2_100, R3_100: 100; R0603
WS2812B_RGB: PINHD-1X3/90; 1X03/90

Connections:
GND: JP1.5, JP1.13, JP1.20, JP2.3, JP2.7, JP2.10, JP2.15, JP2.17, JP3.5, JP3.13, JP3.20, JP4.3, JP4.7, JP4.10, JP4.15, JP4.17, LED1.4 (BLUE_C), LED1.5 (RED_C), LED1.6 (GREEN_C), LED2.4 (BLUE_C), LED2.5 (RED_C), LED2.6 (GREEN_C), LED3.4 (BLUE_C), LED3.5 (RED_C), LED3.6 (GREEN_C), LED4.4 (BLUE_C), LED4.5 (RED_C), LED4.6 (GREEN_C), WS2812B_RGB.2
unnamed: JP2.8, JP4.8, R3_100.1
unnamed: JP1.10, JP3.10
unnamed: JP1.14, JP3.14, R2_100.1
unnamed: JP1.9, JP3.9
unnamed: JP1.3, JP3.3
unnamed: JP1.1, JP3.1
unnamed: JP1.2, JP3.2
unnamed: JP1.4, JP3.4
unnamed: JP1.6, JP3.6
unnamed: JP1.7, JP3.7
unnamed: JP1.8, JP3.8
unnamed: JP1.12, JP3.12
unnamed: JP1.15, JP3.15
unnamed: JP1.16, JP3.16, R1_100.1
unnamed: JP1.18, JP3.18
unnamed: JP1.19, JP3.19
unnamed: JP2.1, JP4.1, WS2812B_RGB.1
unnamed: JP2.2, JP4.2
unnamed: JP2.4, JP4.4
unnamed: JP2.5, JP4.5
unnamed: JP2.6, JP4.6
unnamed: JP2.9, JP4.9
unnamed: JP2.12, JP4.12
unnamed: JP2.13, JP4.13
unnamed: JP2.14, JP4.14
unnamed: JP2.16, JP4.16, WS2812B_RGB.3
unnamed: LED1.3 (BLUE_A), LED2.3 (BLUE_A), LED3.3 (BLUE_A), LED4.3 (BLUE_A), R3_100.2
unnamed: LED1.1 (GREEN_A), LED2.1 (GREEN_A), LED3.1 (GREEN_A), LED4.1 (GREEN_A), R1_100.2
unnamed: LED1.2 (RED_A), LED2.2 (RED_A), LED3.2 (RED_A), LED4.2 (RED_A), R2_100.2
unnamed: JP2.18, JP4.18
unnamed: JP2.19, JP4.19
unnamed: JP2.20, JP4.20
unnamed: JP1.17, JP3.17
unnamed: JP1.11, JP3.11
unnamed: JP2.11, JP4.11

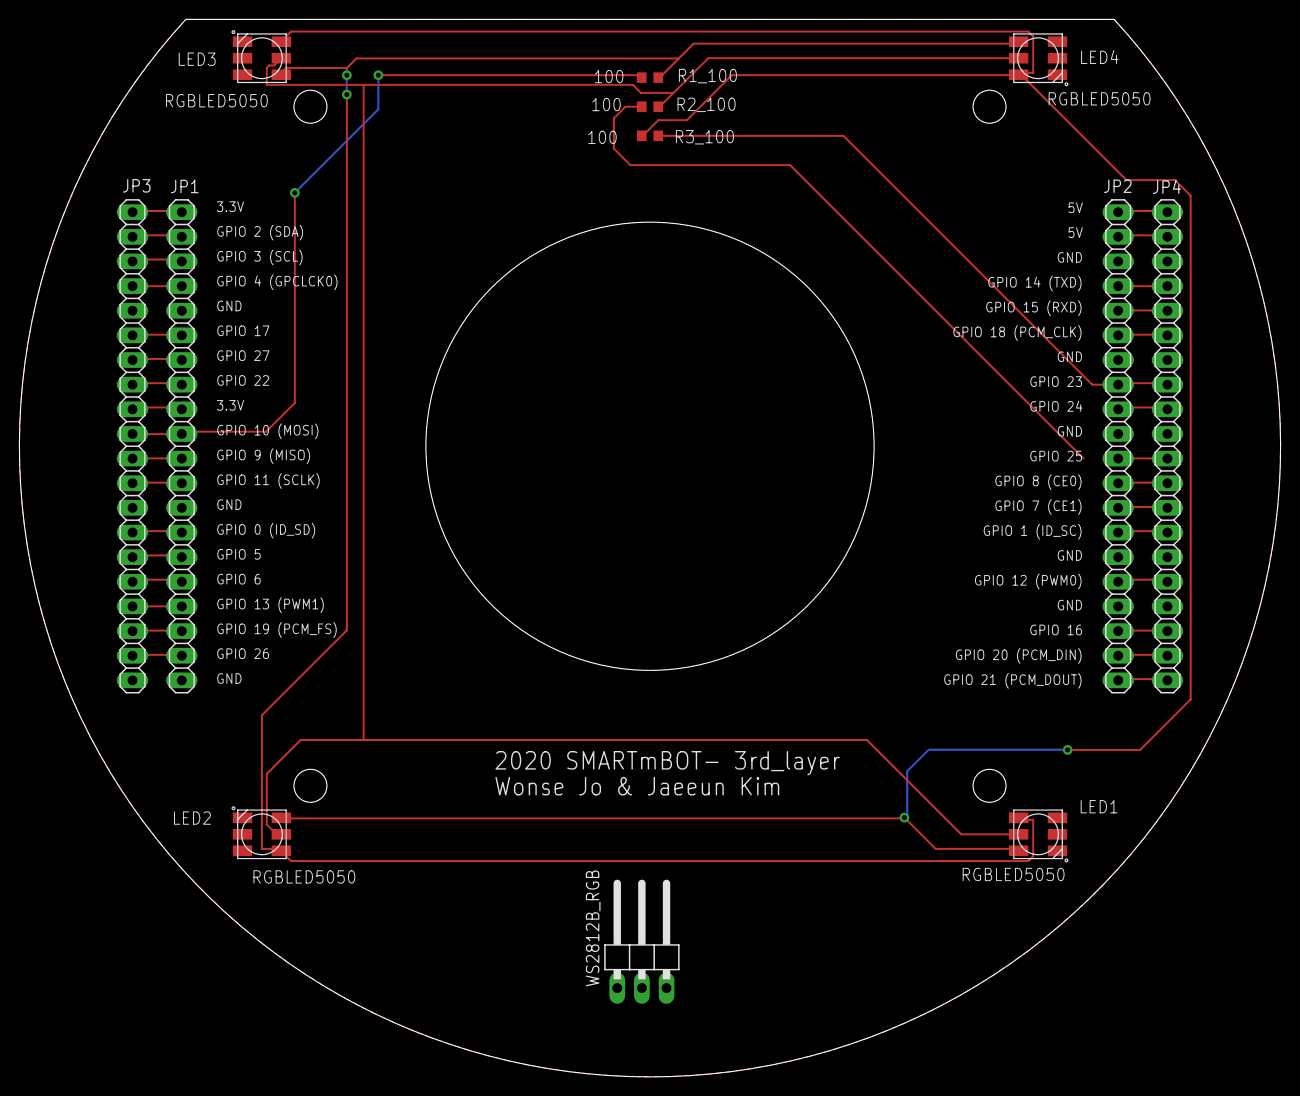
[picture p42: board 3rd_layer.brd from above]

Board: 2 copper layers, 130.0 x 109.0 mm, 12 parts (0 on the bottom side), 36 nets.

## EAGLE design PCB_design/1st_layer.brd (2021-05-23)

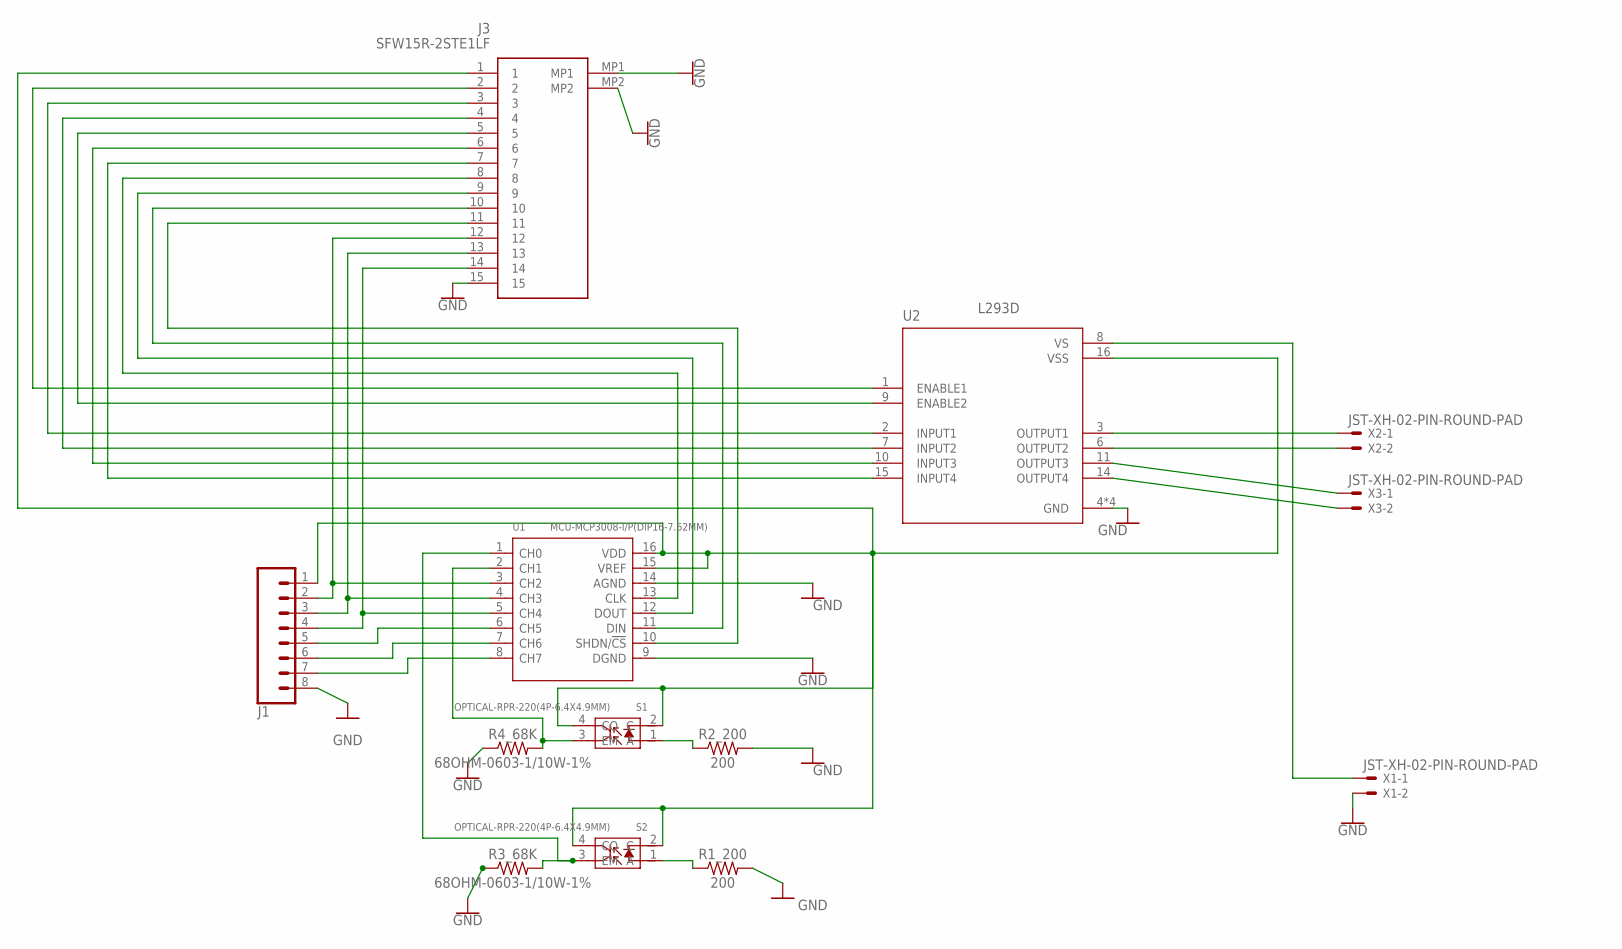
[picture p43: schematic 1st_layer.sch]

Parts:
J1: CONN_08LONGPADS; 1X08_LONGPADS
J3: SFW15R-2STE1LF; SFW15R2STE1LF
R1_200, R2_200: 200; 0603
R3_68K, R4_68K: 68OHM-0603-1/10W-1%; 0603
S1, S2: OPTICAL-RPR-220(4P-6.4X4.9MM); SNR4-8.7X4.5X5.8MM
U1: MCU-MCP3008-I/P(DIP16-7.62MM); DIP16-2.54-19.2X7.62MM
U2: L293D; DIP880W50P254L2000H510Q16
X1, X2, X3: JST-XH-02-PIN-ROUND-PAD; JST-XH-02-PACKAGE-ROUND-PAD

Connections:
GND: J1.8, J3.15, J3.MP1, J3.MP2, R1_200.2, R2_200.2, R3_68K.1, R4_68K.1, U1.9 (DGND), U1.14 (AGND), U2.4 (GND), U2.5 (GND), U2.12 (GND), U2.13 (GND), X1.2
unnamed: R2_200.1, S1.1 (A)
unnamed: R1_200.1, S2.1 (A)
unnamed: U2.8 (VS), X1.1
unnamed: R4_68K.2, S1.3 (EM), U1.2 (CH1)
unnamed: R3_68K.2, S2.3 (EM), U1.1 (CH0)
unnamed: U2.3 (OUTPUT1), X2.1
unnamed: U2.6 (OUTPUT2), X2.2
unnamed: U2.11 (OUTPUT3), X3.1
unnamed: U2.14 (OUTPUT4), X3.2
unnamed: J1.2, J3.12, U1.3 (CH2)
unnamed: J3.3, U2.2 (INPUT1)
unnamed: J3.4, U2.7 (INPUT2)
unnamed: J3.5, U2.9 (ENABLE2)
unnamed: J3.2, U2.1 (ENABLE1)
unnamed: J3.6, U2.10 (INPUT3)
unnamed: J3.7, U2.15 (INPUT4)
unnamed: J3.8, U1.13 (CLK)
unnamed: J3.9, U1.12 (DOUT)
unnamed: J3.10, U1.11 (DIN)
unnamed: J3.11, U1.10 (SHDN/!CS)
unnamed: J1.3, J3.13, U1.4 (CH3)
unnamed: J1.4, J3.14, U1.5 (CH4)
unnamed: J1.5, U1.6 (CH5)
unnamed: J1.6, U1.7 (CH6)
unnamed: J1.7, U1.8 (CH7)
VDD: J1.1, J3.1, S1.2 (C), S1.4 (CO), S2.2 (C), S2.4 (CO), U1.15 (VREF), U1.16 (VDD), U2.16 (VSS)

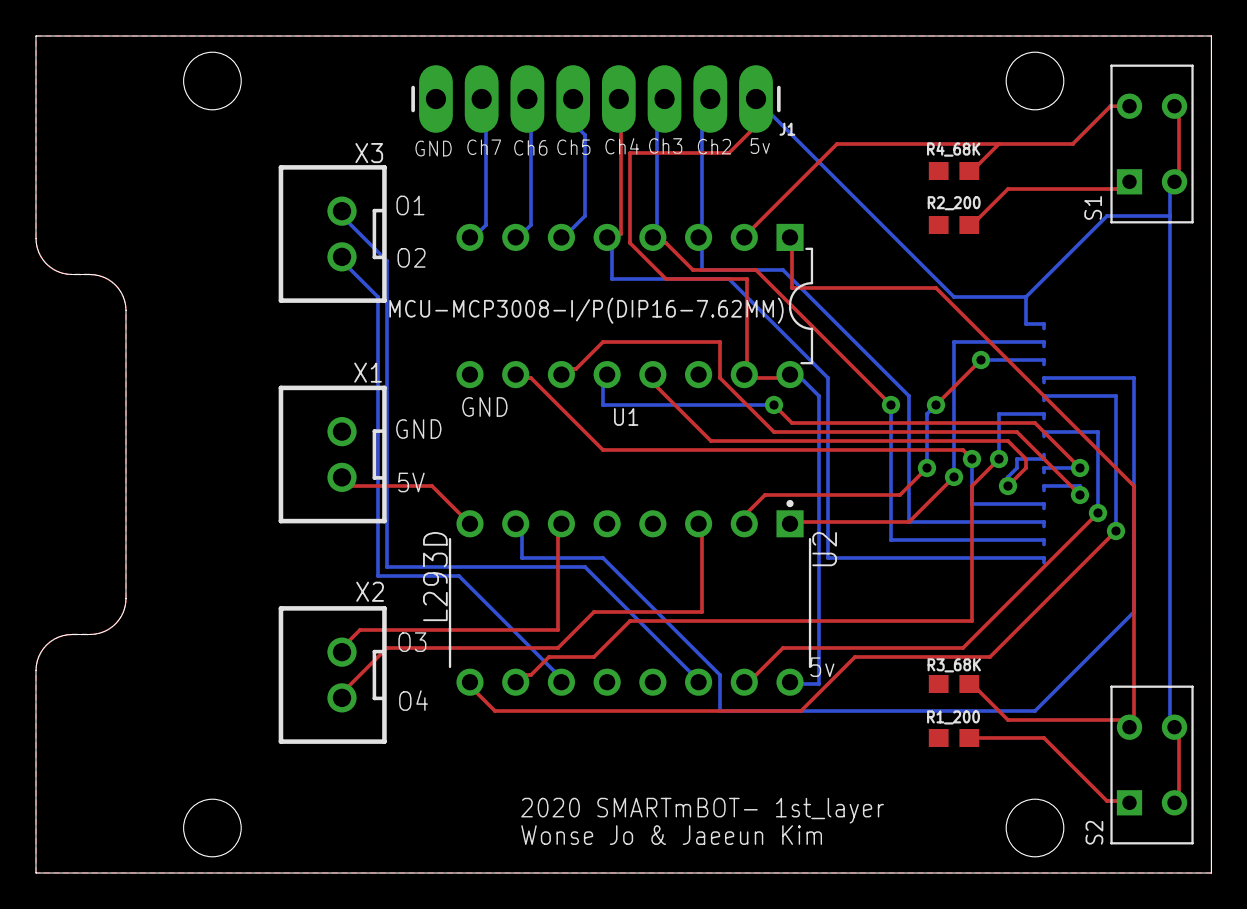
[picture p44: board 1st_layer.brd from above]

Board: 2 copper layers, 65.3 x 46.5 mm, 13 parts (1 on the bottom side), 27 nets.

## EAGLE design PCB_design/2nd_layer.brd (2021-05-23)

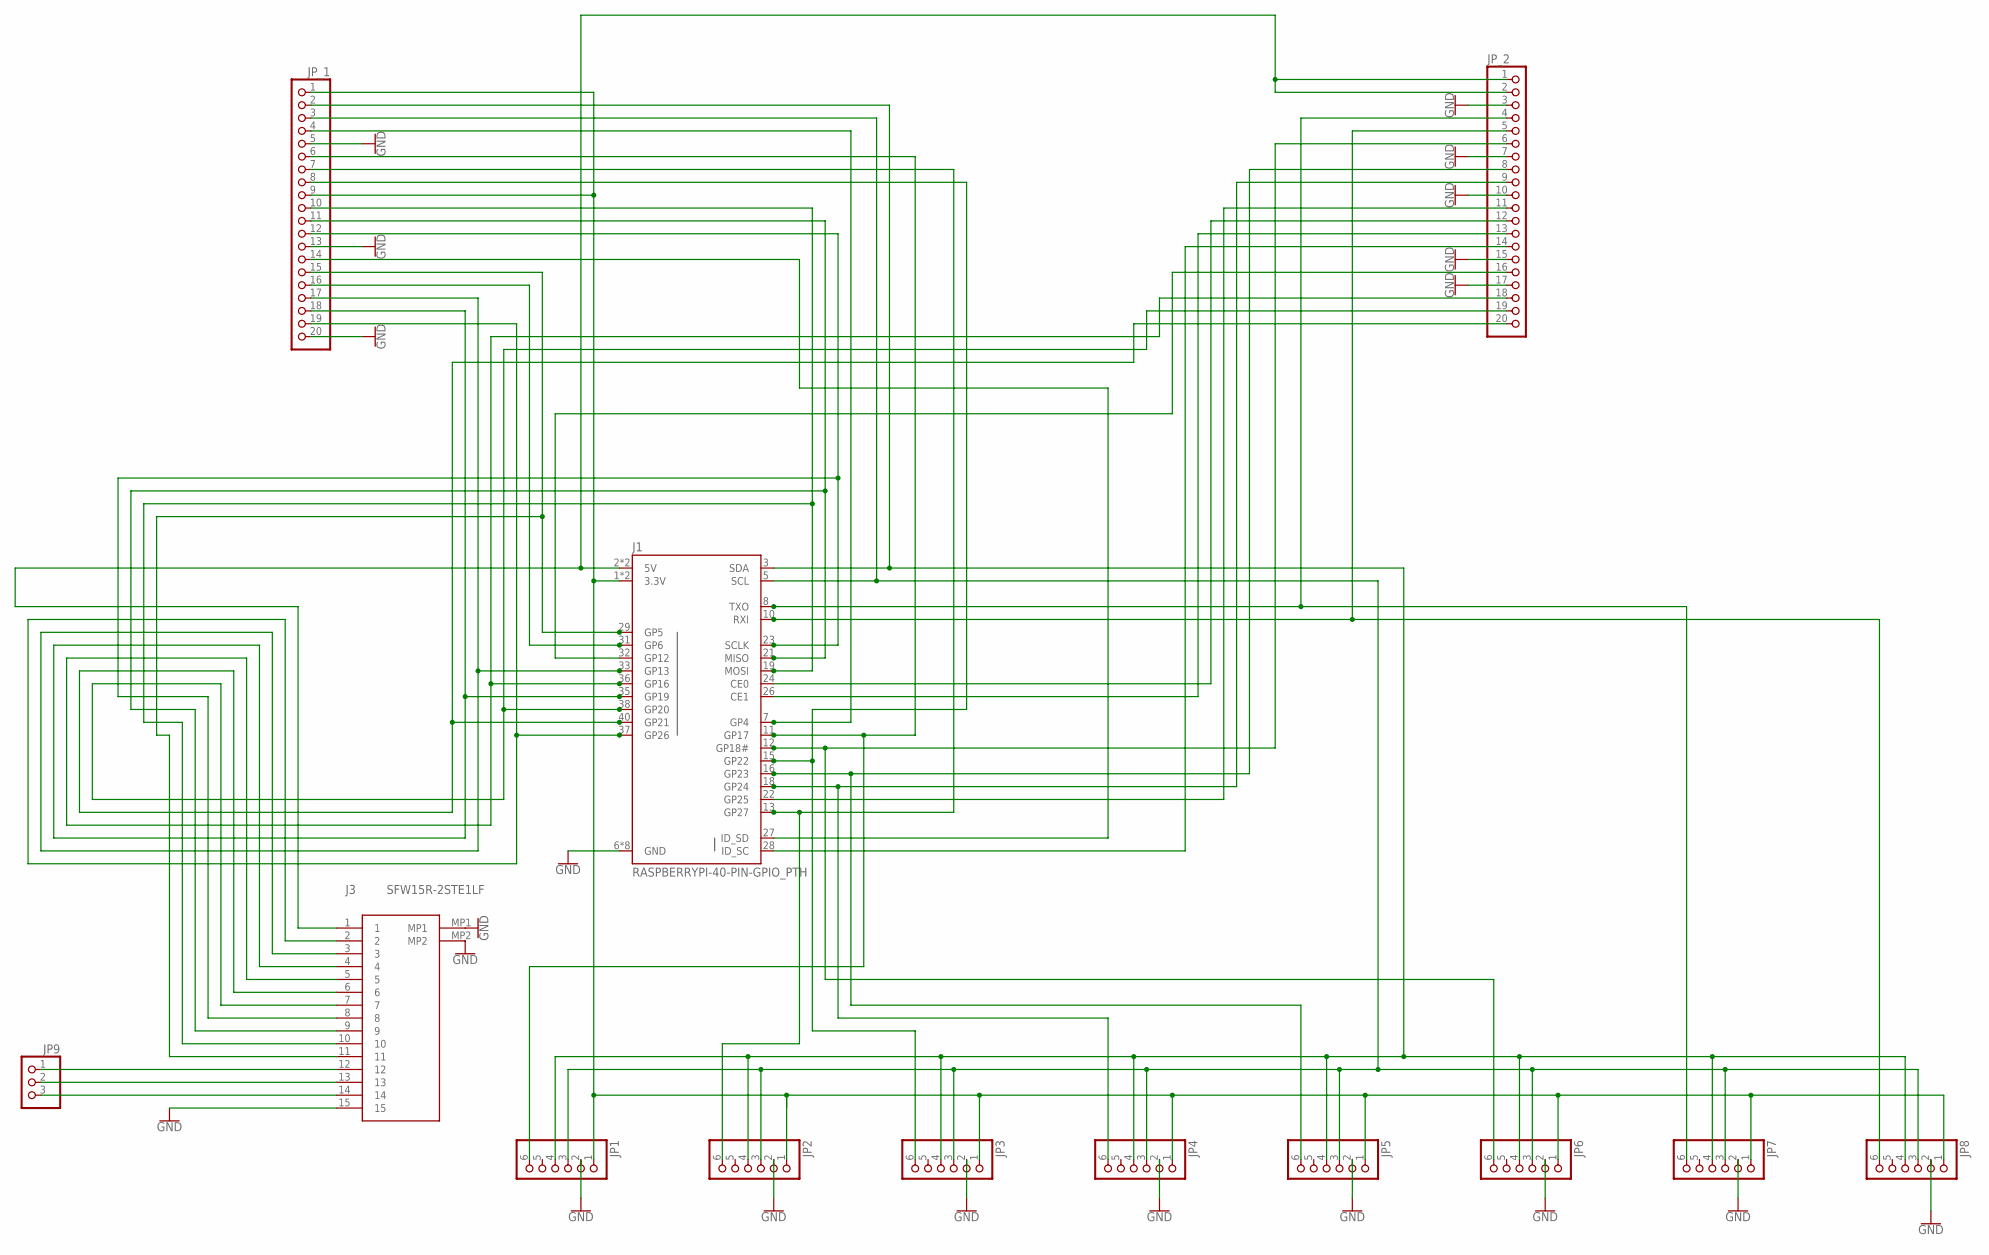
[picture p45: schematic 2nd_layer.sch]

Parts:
J1: RASPBERRYPI-40-PIN-GPIO_PTH; 2X20_SHROUDED
J3: SFW15R-2STE1LF; SFW15R2STE1LF
JP1, JP2, JP3, JP4, JP5, JP6, JP7, JP8: PINHD-1X6; 1X06
JP9: PINHD-1X3; 1X03
JP_1, JP_2: PINHD-1X20; 1X20

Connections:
GND: J1.6 (GND), J1.9 (GND), J1.14 (GND), J1.20 (GND), J1.25 (GND), J1.30 (GND), J1.34 (GND), J1.39 (GND), J3.15, J3.MP1, J3.MP2, JP1.2, JP2.2, JP3.2, JP4.2, JP5.2, JP6.2, JP7.2, JP8.2, JP_1.5, JP_1.13, JP_1.20, JP_2.3, JP_2.7, JP_2.10, JP_2.15, JP_2.17
unnamed: J1.7 (GP4), JP_1.4
unnamed: J1.31 (GP6), JP_1.16
unnamed: J1.22 (GP25), JP_2.11
unnamed: J1.2 (5V), J1.4 (5V), J3.1, JP_2.1, JP_2.2
unnamed: J1.1 (3.3V), J1.17 (3.3V), JP1.1, JP2.1, JP3.1, JP4.1, JP5.1, JP6.1, JP7.1, JP8.1, JP_1.1, JP_1.9
unnamed: J1.27 (ID_SD), JP_1.14
unnamed: J1.5 (SCL), JP1.3, JP2.3, JP3.3, JP4.3, JP5.3, JP6.3, JP7.3, JP8.3, JP_1.3
unnamed: J1.3 (SDA), JP1.4, JP2.4, JP3.4, JP4.4, JP5.4, JP6.4, JP7.4, JP8.4, JP_1.2
unnamed: J1.11 (GP17), JP1.6, JP_1.6
unnamed: J1.13 (GP27), JP2.6, JP_1.7
unnamed: J1.15 (GP22), JP3.6, JP_1.8
unnamed: J1.18 (GP24), JP4.6, JP_2.9
unnamed: J1.16 (GP23), JP5.6, JP_2.8
unnamed: J1.12 (GP18#), JP6.6, JP_2.6
unnamed: J1.8 (TXO), JP7.6, JP_2.4
unnamed: J1.10 (RXI), JP8.6, JP_2.5
unnamed: J1.37 (GP26), J3.2, JP_1.19
unnamed: J1.33 (GP13), J3.3, JP_1.17
unnamed: J1.35 (GP19), J3.4, JP_1.18
unnamed: J1.36 (GP16), J3.5, JP_2.18
unnamed: J1.40 (GP21), J3.6, JP_2.20
unnamed: J1.38 (GP20), J3.7, JP_2.19
unnamed: J1.23 (SCLK), J3.8, JP_1.12
unnamed: J1.21 (MISO), J3.9, JP_1.11
unnamed: J1.19 (MOSI), J3.10, JP_1.10
unnamed: J1.29 (GP5), J3.11, JP_1.15
unnamed: J1.24 (CE0), JP_2.12
unnamed: J1.26 (CE1), JP_2.13
unnamed: J1.28 (ID_SC), JP_2.14
unnamed: J1.32 (GP12), JP_2.16
unnamed: J3.12, JP9.1
unnamed: J3.13, JP9.2
unnamed: J3.14, JP9.3

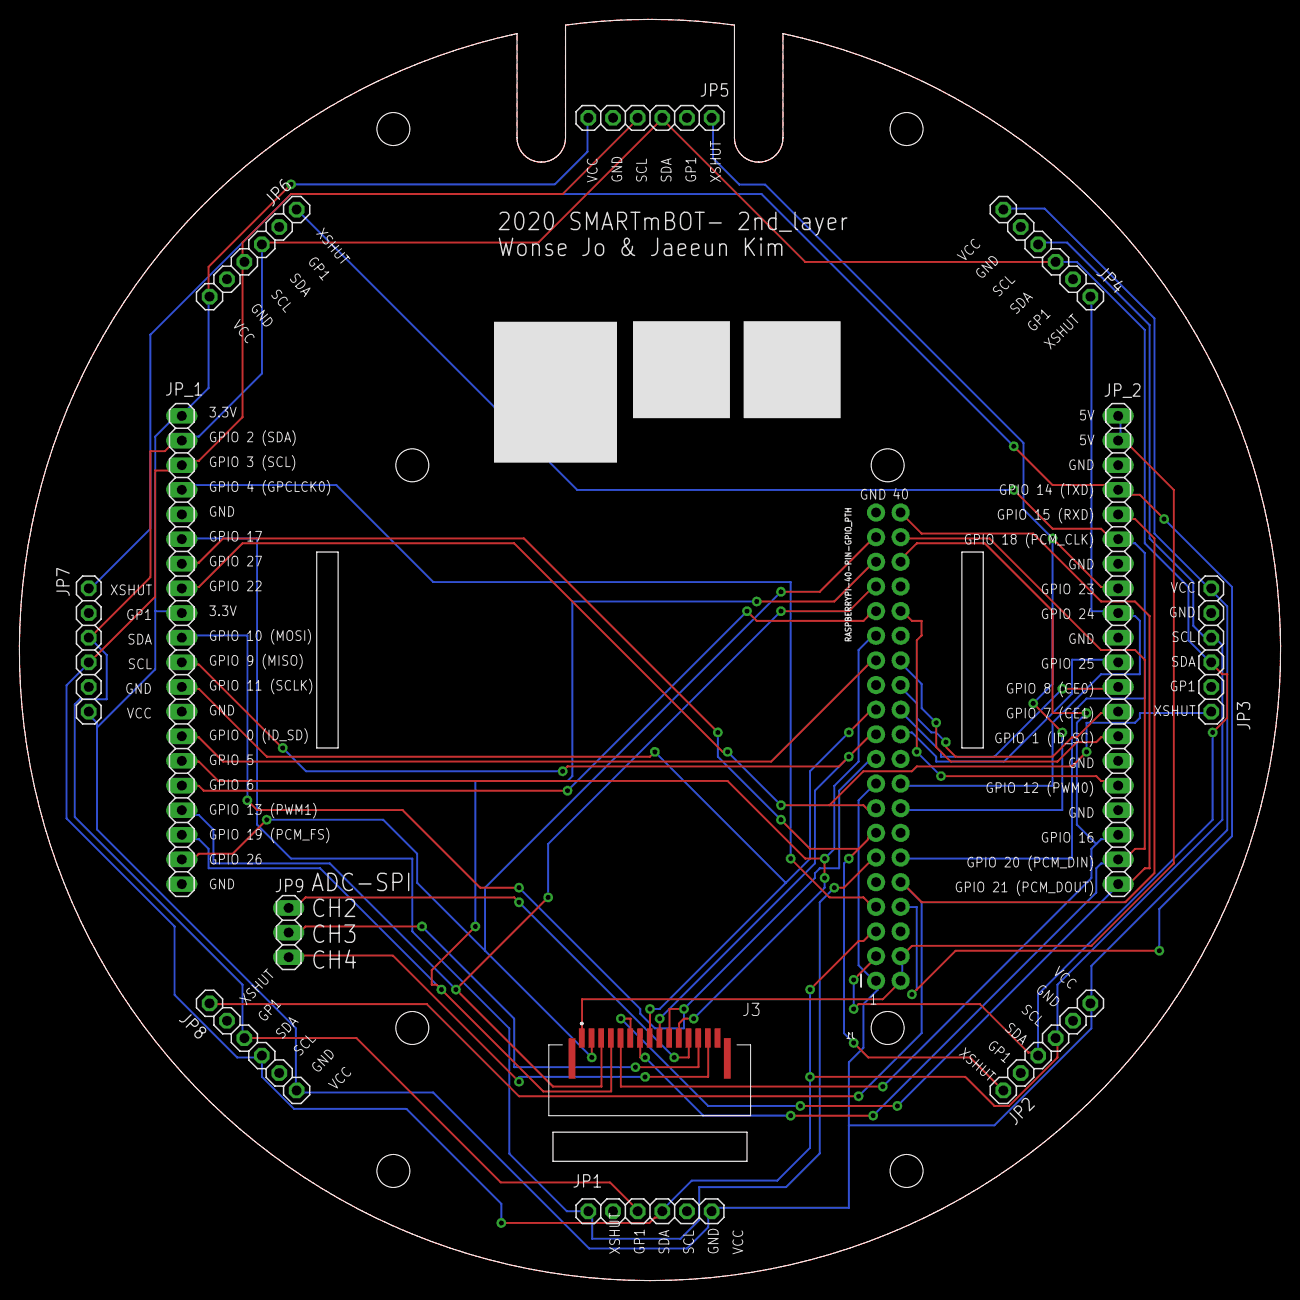
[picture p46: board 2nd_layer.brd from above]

Board: 2 copper layers, 130.0 x 130.0 mm, 13 parts (1 on the bottom side), 34 nets.

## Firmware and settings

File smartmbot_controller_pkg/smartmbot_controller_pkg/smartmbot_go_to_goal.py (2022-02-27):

import rclpy
from rclpy.node import Node

from rclpy.parameter import Parameter

from geometry_msgs.msg import Twist
from std_msgs.msg import String, Int32, Int32MultiArray, Float32MultiArray, MultiArrayLayout, MultiArrayDimension
from vicon_receiver.msg import Position



import sys, math
import numpy as np


class Go_to_Goal_Controller(Node):
    def __init__(self):
        super().__init__('robot_go_to_goal_control_node')
        #====================================================#
        ####  Global Variables in Class                   ####
        #====================================================#
        self.declare_parameter('robot_name', 'smartmbot_1')
        self.param_robot_ID = self.get_parameter('robot_name').value
        #====================================================#
        ####  Global Variables in Class                   ####
        #====================================================#
        #self.human_positions = np.zeros(6)
        self.smartmbot_spi_adc_data = np.zeros(8)
        self.smartmbot_tof_array_data = np.zeros(8)
        self.is_back = 0
        self.right_heavy_for = 0
        self.left_heavy_for = 0
        self.right_heavy_back = 0
        self.left_heavy_back = 0
 
        ####  Robot ID and positions
        self.current_robot_pose = np.zeros(3)
        self.error_robot_pose = np.zeros(3)

        self.current_target_pose = np.zeros(3)
        self.error_target_pose = np.zeros(3)

        #====================================================#
        ####  Subscription Section                        ####
        #====================================================#
        # Reading Human Pose
        #self.sub_human_pose = self.create_subscription(Float32MultiArray, '/smartmbot_host/reading_pose/human', self.sub_human_pose_callback, 10)

        # Reading All Robot Pose
        self.sub_robot_pose = self.create_subscription(Position, '/vicon/'+self.param_robot_ID+'/'+self.param_robot_ID, self.sub_robot_pose_callback, 10)
        
        # Reading All Robot Pose
        target_name = "cup"
        self.sub_target_pose = self.create_subscription(Position, '/vicon/'+target_name+'/'+target_name, self.sub_target_pose_callback, 10)


        # Sub:: SMARTmBOT Robot 1
        self.sub_smartmbot_reading_spi_adc = self.create_subscription(Float32MultiArray, '/'+ self.param_robot_ID+'/reading_spi_adc', self.sub_smartmbot_reading_spi_adc_callback, 10)
        self.sub_smartmbot_reading_tof_array = self.create_subscription(Int32MultiArray, '/'+ self.param_robot_ID+'/reading_tof_array', self.sub_smartmbot_reading_tof_array_callback, 10)


        #====================================================#
        ####  Publisher Section                           ####
        #====================================================#
        # Pub:: SMARTmBOT Robot 1
        print('/'+ self.param_robot_ID+'/writing_dc_motor_vel')
        self.pub_smartmbot_writing_dc_motor_vel = self.create_publisher(Float32MultiArray, '/'+ self.param_robot_ID+'/writing_dc_motor_vel', 10)
        self.pub_smartmbot_writing_gpio_smd5050_led = self.create_publisher(Float32MultiArray, '/'+ self.param_robot_ID+'/writing_gpio_smd5050_led', 10)
        self.pub_smartmbot_writing_ws2813_rgb_strip = self.create_publisher(Float32MultiArray, '/'+ self.param_robot_ID+'/writing_ws2813_rgb_strip', 10)

        self.pub_smartmbot_writing_ws2813_rgb_strip.publish(Float32MultiArray(data=[0.0, 255.0, 0.0, 1.0, 0.5, 0.0, 1.0]))

        smartmbot_controller_timer_period = 0.01  # seconds
        self.smartmbot_controller_timer = self.create_timer(smartmbot_controller_timer_period, self.smartmbot_controller_timer_callback)       
    
    def smartmbot_controller_timer_callback(self):

        # Currnet Robot pose::: [x, y, yaw]  - unit: [mm, mm, rad]
        smartmbot_currnt_pose = self.current_robot_pose
        
        
        # for test
        #print("current:", smartmbot_currnt_pose)
        
        k_linear = 0.02
        k_angular = 0.8
        
        
        (linear_vel, angular_vel)= self.go_to_goal_controller(smartmbot_currnt_pose, self.current_target_pose, k_linear, k_angular)
        
        ### Robot Controller
        wheel_base = 90 # unit: mm   
        wheel_radius = 20 # unit: mm    

        if linear_vel == 0:
            offset = 0
        else:
            offset = 20 # PWM

        print(linear_vel, angular_vel)

        (vL_pwm, vR_pwm) = self.robot_unicycle_controller(linear_vel, angular_vel, wheel_base, wheel_radius, offset)



        if vL_pwm > 100:
            vL_pwm = 100
        if vL_pwm < -100:
            vL_pwm = -100

        if vR_pwm > 100:
            vR_pwm = 100
        if vR_pwm < -100:
            vR_pwm = -100

        #For test
        print(vL_pwm, vR_pwm)
        #vL_pwm = 0.0
        #vR_pwm = 0.0


        #Publish dc motor vels
        msg = Float32MultiArray()

        msg.data = [float(vL_pwm), float(vR_pwm)] # PWM: []
        self.pub_smartmbot_writing_dc_motor_vel.publish(msg)
   

    def go_to_goal_controller(self, current_pos, desired_pos, linear_gain = 1, angular_gain = 2):

        (current_x, current_y, current_theta) = current_pos # Unit: mm
        (goal_x, goal_y, goal_theta) = desired_pos # Unit: radian


        # Go-To-Goal Algorithm        
        distance = math.sqrt(math.pow((current_x-goal_x), 2) + math.pow((current_y-goal_y), 2))
        print("distance:", distance)

        linear = distance * linear_gain
        
        diff_angle = round(math.atan2(goal_y - current_y, goal_x - current_x), 4)
        angular = angular_gain * (diff_angle - current_theta)

        # When robot arrived the trageted position
        if distance <= 150:
            linear = 0
            print("arrived the goal")

           
        else:
            self.pub_smartmbot_writing_ws2813_rgb_strip.publish(Float32MultiArray(data=[0.0, 0.0, 255.0, 1.0, 0.5, 0.0, 1.0]))
        

        linear_velocity = round(linear, 4)
        angular_velocity = 0 #round(angular, 4)

        #print("is back?:", self.is_back)

        return linear_velocity, angular_velocity

   
    def robot_unicycle_controller(self, linear_vel, angular_vel, wheel_base = 90, wheel_radius = 20, offset_pwm = 20):

        left_speed = linear_vel - angular_vel * wheel_base/2
        right_speed = linear_vel + angular_vel * wheel_base/2
        
        left_speed_pwm = int(left_speed + offset_pwm)
        right_speed_pwm = int(right_speed + offset_pwm)
    
        if self.left_heavy_for == 1:
            right_speed_pwm *= 1.2
        elif self.left_heavy_back == 1:
            right_speed_pwm *= 1.2
        elif self.right_heavy_for == 1:
            left_speed_pwm *= 1.2
        elif self.right_heavy_back == 1:
            left_speed_pwm *= 1.2 

        return left_speed_pwm, right_speed_pwm

    def euler_from_quaternion(self, quaternion):
        """
        Converts quaternion (w in last place) to euler roll, pitch, yaw
        quaternion = [x, y, z, w]
        Bellow should be replaced when porting for ROS 2 Python tf_conversions is done.
        """
        x = quaternion[0]
        y = quaternion[1]
        z = quaternion[2]
        w = quaternion[3]

        sinr_cosp = 2 * (w * x + y * z)
        cosr_cosp = 1 - 2 * (x * x + y * y)
        roll = np.arctan2(sinr_cosp, cosr_cosp)

        sinp = 2 * (w * y - z * x)
        pitch = np.arcsin(sinp)

        siny_cosp = 2 * (w * z + x * y)
        cosy_cosp = 1 - 2 * (y * y + z * z)
        yaw = np.arctan2(siny_cosp, cosy_cosp)

        return roll, pitch, yaw #unit: radian

      

    def sub_target_pose_callback(self, msg):
        # Currnet Robot pose::: [x, y, yaw]  - unit: [mm, mm, rad]
        if msg.x_trans != 0:
            self.current_target_pose[0] = msg.x_trans
            self.current_target_pose[1] = msg.y_trans

            input_quat_data = [msg.x_rot, msg.y_rot, msg.z_rot, msg.w]
            [roll, pitch, yaw] = self.euler_from_quaternion(input_quat_data)
            self.current_target_pose[2] = yaw
            self.error_target_pose = self.current_target_pose
        else:
            self.current_target_pose = self.error_target_pose

    def sub_robot_pose_callback(self, msg):
        # Currnet Robot pose::: [x, y, yaw]  - unit: [mm, mm, rad]
        if msg.x_trans != 0:
            self.current_robot_pose[0] = msg.x_trans
            self.current_robot_pose[1] = msg.y_trans

            input_quat_data = [msg.x_rot, msg.y_rot, msg.z_rot, msg.w]
            [roll, pitch, yaw] = self.euler_from_quaternion(input_quat_data)
            self.current_robot_pose[2] = yaw
            self.error_robot_pose = self.current_robot_pose

        else:
            self.current_robot_pose = self.error_robot_pose

    # Sub: For reading sensors of the SMARTmBOT  
    def sub_smartmbot_reading_spi_adc_callback(self, msg):
        try:
            self.smartmbot_spi_adc_data = msg.data
        except:            
            pass
    def sub_smartmbot_reading_tof_array_callback(self, msg):
        try:
            self.smartmbot_tof_array_data = msg.data
        except:
            pass


def main(args=None):
    rclpy.init(args=args)

    robot_go_to_goal_control_node = Go_to_Goal_Controller()

    try:
        while rclpy.ok():
            pass
            rclpy.spin(robot_go_to_goal_control_node)

    except KeyboardInterrupt:
        print('repeater stopped cleanly')
        
    except BaseException:
        print('exception in repeater:', file=sys.stderr)
        raise

    finally:        
        robot_go_to_goal_control_node.destroy_node()
        rclpy.shutdown() 

if __name__ == '__main__':
    main()

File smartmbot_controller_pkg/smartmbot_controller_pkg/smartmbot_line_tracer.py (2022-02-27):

import rclpy
from rclpy.node import Node

from rclpy.parameter import Parameter

from geometry_msgs.msg import Twist
from std_msgs.msg import String, Int32, Int32MultiArray, Float32MultiArray

import sys, math
import numpy as np

class controller_irb_cctv_line_follower(Node):
    def __init__(self):
        super().__init__('robot_irb_leader_follower_node')
        #====================================================#
        ####  Global Variables in Class                   ####
        #====================================================#
        self.declare_parameter('robot_name', 'smartmbot_4')
        self.declare_parameter('moving_speed', 30)
        self.declare_parameter('adc_threshold', 1.5)
        self.declare_parameter('adc_threshold_back', 1.5)

        self.param_robot_ID = self.get_parameter('robot_name').value
        self.param_robot_speed = self.get_parameter('moving_speed').value
        self.param_adc_threshold = self.get_parameter('adc_threshold').value
        self.param_adc_threshold_back = self.get_parameter('adc_threshold_back').value
        #====================================================#
        ####  Global Variables in Class                   ####
        #====================================================#
        self.human_positions = np.zeros(6)
        self.all_smartmbot_positions = np.zeros((20, 6))
        self.smartmbot_spi_adc_data = np.zeros(8)
        self.smartmbot_tof_array_data = np.zeros(8)
        self.cctv_experiment_command = 0

        self.robot_direction = True # True = Forward, False = Backward

        self.robot_ID_array = ['smartmbot_1', 'smartmbot_2', 'smartmbot_3', 'smartmbot_4', 'smartmbot_5', 'smartmbot_6', 'smartmbot_7', 'smartmbot_8', 'smartmbot_9', 'smartmbot_10', 'smartmbot_11', 'smartmbot_12', 'smartmbot_13', 'smartmbot_14', 'smartmbot_15', 'smartmbot_16', 'smartmbot_17', 'smartmbot_18', 'smartmbot_19', 'smartmbot_20']
        
        #====================================================#
        ####  Subscription Section                        ####
        #====================================================#
        # Reading Human Pose
        #self.sub_human_pose = self.create_subscription(Float32MultiArray, '/smartmbot_host/reading_pose/human', self.sub_human_pose_callback, 10)
        # Reading All Robot Pose
        #self.sub_all_robot_pose = self.create_subscription(Float32MultiArray, '/smartmbot_host/reading_pose/robots', self.sub_all_robot_pose_callback, 10)
       

        # Sub:: SMARTmBOT Robots
        self.sub_smartmbot_reading_spi_adc = self.create_subscription(Float32MultiArray, '/'+self.param_robot_ID+'/reading_spi_adc', self.sub_smartmbot_reading_spi_adc_callback, 10)
        self.sub_smartmbot_reading_tof_array = self.create_subscription(Int32MultiArray, '/'+ self.param_robot_ID+'/reading_tof_array', self.sub_smartmbot_reading_tof_array_callback, 10)
        
        # Sub:: User Study Status
        self.sub_cctv_experiment_command = self.create_subscription(Int32, '/cctv_GUI/control_state', self.sub_cctv_experiment_command_callback, 10)
        #Example: self.pub_cctv_GUI_control_state.publish(Int32(data=1))
        # data = 0 ------>  Start the mission and go to Prep. session
        # data = 1 ------>  Showing CCTV cameras
        # data = 2 ------>  SAM Question
        # data = 3 ------>  NASA-TLX Question
        # data = 4 ------>  End the mission


        #=======================
        # =============================#
        ####  Publisher Section                           ####
        #====================================================#
        # Pub:: User Study Status

        # Pub:: SMARTmBOT Robot 1
        print('/'+ self.param_robot_ID+'/writing_dc_motor_vel')
        self.pub_smartmbot_writing_dc_motor_vel = self.create_publisher(Float32MultiArray, '/'+ self.param_robot_ID+'/writing_dc_motor_vel', 10)
        self.pub_smartmbot_writing_gpio_smd5050_led = self.create_publisher(Float32MultiArray, '/'+ self.param_robot_ID+'/writing_gpio_smd5050_led', 10)
        self.pub_smartmbot_writing_ws2813_rgb_strip = self.create_publisher(Float32MultiArray, '/'+ self.param_robot_ID+'/writing_ws2813_rgb_strip', 10)

        smartmbot_controller_timer_period = 0.01  # seconds
        self.smartmbot_controller_timer = self.create_timer(smartmbot_controller_timer_period, self.smartmbot_controller_timer_callback)       


    def smartmbot_controller_timer_callback(self):
        follow_robot_ID_index = self.robot_ID_array.index(self.param_robot_ID)
        
        user_study_state = self.cctv_experiment_command

        if user_study_state == 0:
            print("Ready, and current PWMs are: ", self.param_robot_speed)
            # self.cctv_experiment_command == 0  --> Ready to begin the study      
            self.pub_smartmbot_writing_ws2813_rgb_strip.publish(Float32MultiArray(data=[0., 0., 255.0, 3., 0.5, 0., 1.]))
            vL_pwm = 0
            vR_pwm = 0     

        elif user_study_state == 1:
            # self.cctv_experiment_command == 1  --> Start the study
            self.pub_smartmbot_writing_ws2813_rgb_strip.publish(Float32MultiArray(data=[0., 0., 0., 1., 0.5, 0., 1.]))

            spi_left = self.smartmbot_spi_adc_data[0]
            spi_right = self.smartmbot_spi_adc_data[1]
            
            spi_right_back = self.smartmbot_spi_adc_data[2]
            spi_left_back = self.smartmbot_spi_adc_data[3]


            tof_front = self.smartmbot_tof_array_data[0]
            tof_right = self.smartmbot_tof_array_data[2]
            tof_back = self.smartmbot_tof_array_data[4]
            tof_left = self.smartmbot_tof_array_data[6]
            
            tof_max_distance = 500

            robot_moving_speed = self.param_robot_speed
            adc_threshold = 1.4

            if spi_right > adc_threshold and spi_left > adc_threshold: #Go Front
                vL_pwm = robot_moving_speed
                vR_pwm = robot_moving_speed
            elif spi_right < adc_threshold and spi_left > adc_threshold: #Go Left
                vL_pwm = robot_moving_speed
                vR_pwm = 0
            elif spi_right > adc_threshold and spi_left < adc_threshold: #Go Right
                vL_pwm = 0
                vR_pwm = robot_moving_speed
            elif spi_right < adc_threshold and spi_left < adc_threshold: # Stop
                if tof_left > tof_max_distance:
                    vL_pwm = 0
                    vR_pwm = 0
                    print("DONE_DONE_DONE_DONE")
                else: 
                    return
                #self.pub_cctv_experiment_command.publish(Int32(data=0))

                
            print("speed:", robot_moving_speed, vL_pwm, vR_pwm, spi_left, spi_right)
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

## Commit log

2021-05-23 moved all file from the Purdue git
    [12x1_male_header_pin.SLDASM, 12x1_male_header_pin_AP203.SLDASM, 12x1_male_header_pin_AP203.STEP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]
2021-05-26 deleted slddrw files
    [2nd_layer.SLDDRW, 3rd_layer.SLDDRW, 3rd_layer.sldprt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]

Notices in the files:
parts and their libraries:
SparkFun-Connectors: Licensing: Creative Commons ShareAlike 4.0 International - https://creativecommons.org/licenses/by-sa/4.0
